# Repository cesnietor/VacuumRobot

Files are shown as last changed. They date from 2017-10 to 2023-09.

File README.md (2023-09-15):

# VacuumRobot
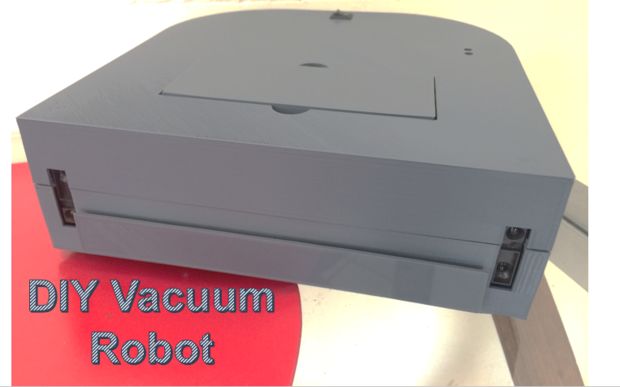
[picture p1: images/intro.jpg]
DIY VacuumRobot


# Created by César Nieto
DIY Vacuum Robot project
An open source project designed to get into the robotics and programming (it is not needed to know how to program).
The full instructions on how to build the robot are on Instructables: 
  https://www.instructables.com/id/Build-Your-Own-Vacuum-Robot/ 

This is my first Vacuum Robot, which it's main purpose is to allow anyone to have a cleaning robot without paying so much money, to learn how they work, to build a nice robot that you can modify, update and program as much as you want, and of course to vacuum all that annoying fluff.

This project is intended to be as easy to build as possible since all the elements and parts are easy to find on Digikey, eBay, Amazon, etc.

The whole chassis was designed in Solidworks so that it could be 3d printed.

Currently it uses an Arduino Uno (if you don't like it too much you can easily change it for another micro controller, I decided to use this since my objective is that anyone could actually build it), micro-metal motors, fan propeller, infrared sensors and respective driver modules.

Another one bites the dust!

Instructions
=====

Step 1: Materials
-----
So, first I will define all the materials that I used and later I will suggest other options with a similar behavior.

**Controllers:**

* 1 x Arduino Uno Board (or similar) ([DigiKey](http://www.digikey.com/product-detail/en/arduino/A000066/1050-1024-ND/2784006))
* 1 x IRF520 MOS FET Driver Module ([Aliexpress](https://aliexpress.com/store/product/0-24VTop-Mosfet-Button-IRF520-MOS-Driver-Module-For-Arduino-MCU-ARM-Raspberry-pie/1185416_32275524365.html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,searchweb201602_3_10000560_10000073_10000561_10000074_10000175_10000507_10000401_10000505_10000068_10000063_10099_10000156_10096_10000569_10000097_10000094_10000090_10000091_10000147_10000144_10084_10000150_10083_10080_10000153_10082_10081_10110_10111_10112_10113_10000535_10114_10000534_10000089_10000086_10000083_10000135_10000080_10078_10079_10073_10000140_10070_10122_10123_10126_10124_10000546_10065_10068_10501_10000132_10000033_10503_10000030_10000126_10000026_10000129_10000023_10000123_432_10060_10062_10056_10055_10054_302_10059_10000120_10000020_10000117_10000013_10103_10102_10000016_10000114_10000111_10052_10053_10050_10107_10051_10106_10000621_10000384_10000101_10000100_10000579_10000104_10000045_10000578_10000108_10000612_10000613_10000390_10000042_10000592_10000039_10000587_10000036_10000389_10000187-10503_10501,searchweb201603_2,afswitch_1,ppcSwitch_4,single_sort_1_default&btsid=23d4dbb7-b390-4b6d-8de8-456e740343d8&algo_expid=c1fe14ed-efb6-4d8b-8aa1-2ef2a833c598-5&algo_pvid=c1fe14ed-efb6-4d8b-8aa1-2ef2a833c598))
* 1 x H-bridge L298 Dual Motor Driver ([Aliexpress](https://aliexpress.com/store/product/Dual-H-Bridge-DC-Stepper-Motor-Drive-Controller-Board-Module-L298N/712084_32273246252.html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,searchweb201602_3_10000560_10000073_10000561_10000074_10000175_10000507_10000401_10000505_10000068_10000063_10099_10000156_10096_10000569_10000097_10000094_10000090_10000091_10000147_10000144_10084_10000150_10083_10080_10000153_10082_10081_10110_10111_10112_10113_10000535_10114_10000534_10000089_10000086_10000083_10000135_10000080_10078_10079_10073_10000140_10070_10122_10123_10126_10124_10000546_10065_10068_10501_10000132_10000033_10503_10000030_10000126_10000026_10000129_10000023_10000123_432_10060_10062_10056_10055_10054_302_10059_10000120_10000020_10000117_10000013_10103_10102_10000016_10000114_10000111_10052_10053_10050_10107_10051_10106_10000621_10000384_10000101_10000100_10000579_10000104_10000045_10000578_10000108_10000612_10000613_10000390_10000042_10000592_10000039_10000587_10000036_10000389_10000187-10503_10501,searchweb201603_2,afswitch_1,ppcSwitch_4,single_sort_1_default&btsid=41cc97c3-c03d-4f3a-9b5a-d7c7f16f9c39&algo_expid=c5bd03f1-c8e0-4179-81da-6a2f469cb3b0-4&algo_pvid=c5bd03f1-c8e0-4179-81da-6a2f469cb3b0))

**Actuators:**

* 2 x Micro Metal Gearmotor HP 6V 298:1 ([DigiKey](http://www.digikey.com/product-detail/en/sparkfun-electronics/ROB-12285/1568-1161-ND/5673747))
* 1 x Micro Metal Gearmotor Bracket Pair ([Pololu](https://www.pololu.com/product/1086))
* 1 x Wheel 42×19mm Pair ([DigiKey](http://www.digikey.com/product-detail/en/sparkfun-electronics/ROB-08899/ROB-08899-ND/5814304))
* 1 x Fan Blower AVC BA10033B12G 12V or similar (BCB1012UH Neato's motor) ([Ebay](http://www.ebay.com/itm/1pc-AVC-BA10033B12G-fan-9733-12V-4-5A-4pin-M3529-QL-/182281112508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), [NeatoOption](http://www.ebay.com/itm/Neato-Vacuum-Fan-and-motor-Impeller-xv-Series-xv-11-xv-14-xv-15-xv-12-xv-21-/201157367856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))

**Sensors:**

* 2 x Sharp Distance Sensor GP2Y0A41SK0F (4 - 30cm) ([DigiKey](http://www.digikey.com/product-detail/en/sharp-microelectronics/GP2Y0A41SK0F/425-2819-ND/3884447))

**Power:**

* 1 x ZIPPY Compact 1300mAh 3S 25C Lipo Pack ([HobbyKing](https://hobbyking.com/en_us/zippy-compact-1300mah-3s-25c-lipo-pack.html))
* 1 x LiPo Battery Charger 3s ([Amazon-Charger](https://www.amazon.com/Turnigy-Compact-Lipo-Charger-100-240v/dp/B00XU4ZR06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))
* 1 x 1k Ohm resistor
* 1 x 2k Ohm small potentiometer

**3d Printing:**

* 3D printer with a minimum printing size of 21 L x 21 W cm .
* PLA Fillament or similar.
* If you don't have, you can print your file on [3DHubs](https://www.3dhubs.com/3dprint).

**Other materials:**

* 20 x M3 bolts with (3mm diameter)
* 20 x M3 nuts
* 2 x #8-32 x 2 IN bolts with nuts and washer.
* 1 x Vaccum bag filter (cloth type)
* 1 x Ball Caster with 3/4″ Plastic or Metal Ball ([Pololu](https://www.pololu.com/product/955))
* 2 pushbuttons
* 1 x On/Off Switch

**Tools:**

* Screw driver
* Soldering Iron
* Pliers
* Scissors
* Cable (3m)

Awesome people share!

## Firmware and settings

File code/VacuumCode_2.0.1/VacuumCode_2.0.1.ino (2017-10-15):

//Code: VaccumCode
//Version: 2.0.1
//Author: Cesar Nieto refer to ces.nietor@gmail.com
//Last change: 19/05/2017
//Changes: Documentation added
#include <math.h> 
////////////PINS////////////////
//Distance Analog Sensors (Sharp)
const int SD1 = 0; //left front sensor
const int SD2 = 1; //right front sensor
const int SD3 = 2; //left side sensor
const int SD4 = 3; //right side sensor

//Battery Voltage input
const int battery = 4;

//IndicatorLED
const int led = 13;

//Fan output
const int fanmotor =  12;      // the number of the LED pin

// Motor1 Right
const int motor1Pin1 = 3;
const int motor1Pin2 = 5;

// Motor2 Left
const int motor2Pin1 = 6;
const int motor2Pin2 = 9;

//Bumper
const int bumper1 = 10;
const int bumper2 = 11;

///////////////Constants////////////////
const float voltageBatCharged = 12.68; // Voltage measured when battery fully charged //Change this
//PWM for the micro metal motors
const int pwmMax = 160;// for 12V  pwmMAx = 170, for 10V output  pwmMax = 140
const int pwmMin = 70;;// for 9V  pwmMin = 128
//Mínimun distance of the sensor
const int minSharp = 30;

// Variables will change:
int bumperState = 0;  // variable for reading the pushbutton status
boolean control = true;
int counter = 0; //   Prevents from being stuck

//////////////CODE/////////////
void setup() {
  //Initialize outputs and inputs
  //Fan motor as output
  pinMode(fanmotor, OUTPUT);
  //Motor1
  pinMode(motor1Pin1, OUTPUT);
  pinMode(motor1Pin2, OUTPUT);
  //Motor2
  pinMode(motor2Pin1, OUTPUT);
  pinMode(motor2Pin2, OUTPUT);
  //LED
  pinMode(led, OUTPUT);
  //INPUTS
  // initialize the pushbutton inputs 
  //Bumper
  pinMode(bumper1, INPUT_PULLUP); 
  pinMode(bumper2, INPUT_PULLUP); 
  //Sensor
  pinMode(SD1, INPUT);
  pinMode(SD2, INPUT);
  pinMode(SD3, INPUT);
  pinMode(SD4, INPUT);
  //Batt
  pinMode(battery, INPUT);
  // Initialize serial
  Serial.begin(9600);    
  ///////////////////////////////Wait////////////////////////////////////////
  //Wait about 5 s and initialize fan if voltage ok
  waitBlinking(5,1); //5 seconds at 1 Hz
  //Crank (initialize the fan because the voltage drops when cranking)
  if(readBattery(battery)>12.1){
    digitalWrite(fanmotor, HIGH); //Turn the Fan ON
    delay(1000); //For 1000ms
  }
  else {
    //do nothing Convention
    }
} 
//////////Functions To Use //////////
void waitBlinking(int n, int frequency){
  //blink for n seconds at frequency hz
  for (int i=1; i <= n; i++){
    for(int j=1; j<=frequency; j++){
      digitalWrite(led, HIGH);   
      delay((1000/frequency)/2);   //Half time on            
      digitalWrite(led, LOW);   
      delay((1000/frequency)/2);   //Half time off
    }
   } 
}
double sdSHARP(int Sensor){
  //Returns the distance in cm
  double dist = pow(analogRead(Sensor), -0.857); // x to power of y
  return (dist * 1167.9);
}
void forwardMotors(int moveTime){  
  //Manipulate direction according the desired movement of the motors
   analogWrite(motor1Pin1, pwmMin); 
   analogWrite(motor1Pin2, 0); //PWM value wher 0 = 0% and 255 = 100%
   analogWrite(motor2Pin1, pwmMin); 
   analogWrite(motor2Pin2, 0); 
   delay(moveTime);
}
void rightMotors(int moveTime){ 
   analogWrite(motor1Pin1, 0); 
   analogWrite(motor1Pin2, pwmMin); 
   analogWrite(motor2Pin1, pwmMin);
   analogWrite(motor2Pin2, 0); 

   delay(moveTime);
}
void leftMotors(int moveTime){ 
   analogWrite(motor1Pin1, pwmMin); 
   analogWrite(motor1Pin2, 0); 
   analogWrite(motor2Pin1, 0);
   analogWrite(motor2Pin2, pwmMin+20); 
   delay(moveTime);
}
void backwardMotors(int moveTime){
   analogWrite(motor1Pin1, 0); 
   analogWrite(motor1Pin2, pwmMin+20);
   analogWrite(motor2Pin1, 0); 
   analogWrite(motor2Pin2, pwmMin+20); 
   delay(moveTime);
}
void stopMotors(){ 
   analogWrite(motor1Pin1, 0);
   analogWrite(motor1Pin2, 0); 
   analogWrite(motor2Pin1, 0); 
   analogWrite(motor2Pin2, 0); 
}
float  readBattery(int input){
  int readInput;
  float voltage;
  readInput = analogRead(input);
  voltage = (((readInput*4.9)/1000)*voltageBatCharged ) / 5; // resolution of analog input = 4.9mV per Voltage 
  Serial.print(" Battery= ");
  Serial.print(voltage);
  return voltage;
  } 
void batteryControl(int input){
  //Turn everything off in case the battery is low
  float v_battery;
  v_battery = readBattery(input);
  if(v_battery<=11.6){ //battery limit of discharge, Don't put this limit lower than  11.1V or you can kill the battery
    control = false;
    }
  else {
    //Do nothing Convention
    }
}
/////////////////////////////////////////////////MAIN CODE//////////////////////////////
void loop(){
  /*  
  Serial.print("SD1= ");
  Serial.print(sdSHARP(SD1));
  Serial.println();
  Serial.print("  SD2= ");
  Serial.print(sdSHARP(SD2));
  Serial.println();
  delay(200);*/
  bumperState = digitalRead(bumper1);
  //Keep the control of the battery automatically turn the fan off
  //If control = true the battery level is ok, otherwise the battery is low.
  batteryControl(battery); //modifies the variable control of the battery is low
  
  if (control){
    digitalWrite(led, HIGH);
    if (sdSHARP(SD1)<=4.3 ){ 
      //If the distance between an object and the left front sensor is less than 4.3 cm or the bumper hits, it will move to the left
      if (counter ==2){ // prevent of being stuck on corners
        counter = 0;
        }
      else {
        //Do nothing Convention
      }
      forwardMotors(100); // approach a bit
      backwardMotors(500); // backward delay of 500ms
      leftMotors(300);
      counter = counter + 2;
      Serial.print("  Turn Left ");
      }
    else if (sdSHARP(SD2)<=4.3){ 
      //If the distance between an object and the right front sensor is less than 4.3 cm, it will move to the right
      if (counter ==1){
        counter = 0;
        }
      else{
        //Do nothing Convention
      }
      forwardMotors(100);
      backwardMotors(500);
      rightMotors(300);
      counter++;
      Serial.print("  Turn Right");
      }
    else if (bumperState==0){
      counter = 0;
      backwardMotors(500); //backward delay of 500ms
      leftMotors(300);
      Serial.print("  Turn Left ");
      }
    else {
      if(counter==3){ //Corner
        leftMotors(1000);
        counter = 0;
        }
      else {
        forwardMotors(0);
      }
      Serial.print("  Move Forward");
      }
  }
  else if (!control){
    //If the battery is low, turn everything off
    digitalWrite(fanmotor, LOW); //Turn the Fan OFF
    stopMotors();
    Serial.print(" Low Battery! ");
    Serial.println();
    waitBlinking(1,3);  //blink as warning 3hz in a loop
    }
  Serial.println();
}

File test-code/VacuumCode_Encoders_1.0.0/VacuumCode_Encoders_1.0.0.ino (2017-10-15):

//Code: VaccumCode_Encoders
//Version: 1.0.0
//Author: Cesar Nieto refer to ces.nietor@gmail.com
//Last change: 04/10/2017
//Last Changes: Code added to support Pololu Motor Encoders, pins have been changed.
//              A PD controller is used to control the speed of the motors.                
#include <math.h> 
////////////PINS////////////////
// Distance Analog Sensors (Sharp)
#define SD1     (0)   //left front sensor
#define SD2     (1)   //right front sensor
#define SD3     (2)   //left side sensor
#define SD4     (3)   //right side sensor
// Battery Voltage input
#define battery     (4)   //Analog
// IndicatorLED
#define led         (13)
// Fan output
#define fanmotor    (12)  // the number of the LED pin
// Motor1 Right
#define motor1Pin1  (9)
#define motor1Pin2  (10)
#define encodPinA1  (2)   // encoder A pin, interrupt pin of Arduino Uno
#define encodPinB1  (4)   // encoder B pin, read motor direction
// Motor2 Left
#define motor2Pin1  (5)
#define motor2Pin2  (6)
#define encodPinA2  (3)   // encoder A pin, interrupt pin of Arduino Uno
#define encodPinB2  (7)   // encoder B pin, read motor direction
// Bumper
#define bumper1     (8)
#define bumper2     (11)
// PWM for the micro metal motors //Values to delete soon since use of PID
#define pwmMax      (160) 
#define pwmMin      (0)  
// PID loop time
#define LOOPTIME  (100)                     

///////////////Constants////////////////
const float voltageBatCharged = 12.68; // Voltage measured when battery fully charged //Change this
const float batteryLimitDischarge = 11.6; // Safe value to not kill the Battery

// Variables will change:
int bumperState = 0;  // variable for reading the pushbutton status
int counter = 0; //   Prevents from being stuck
boolean control = true;
boolean printOnce = true; //For debugging

unsigned long lastMilli = 0;    // loop timing 
unsigned long lastMilliPrint = 0;
unsigned long lastErrorMilli = 0;
//Motor 1
float speed_req1 = 60.0;            // speed (Set Point)
float speed_act1 = 0.0;             // speed (actual value)
int PWM_val1 = 0;               // (25% = 64; 50% = 127; 75% = 191; 100% = 255)
volatile long count_1 = 0;      // rev counter
//Motor 2
float speed_req2 = 60.0;
float speed_act2 = 0.0;
int PWM_val2 = 0;
volatile long count_2 = 0;

float Kp =   0.6;// 0.65;        // PID Proportional control Gain   (Good values as well: 0.5)     
float Kd =   0.0;// 0.005;       // PID Derivitave control Gain

//////////////CODE/////////////
void setup() {
  Serial.begin(9600); // Initialize serial
  //Initialize outputs and inputs
  //Fan motor as output
  pinMode(fanmotor, OUTPUT);
  //Motor1
  pinMode(motor1Pin1, OUTPUT);
  pinMode(motor1Pin2, OUTPUT);
  //Motor2
  pinMode(motor2Pin1, OUTPUT);
  pinMode(motor2Pin2, OUTPUT);
  //LED
  pinMode(led, OUTPUT);
  //INPUTS
  //Initialize the pushbutton inputs 
  //Motor encoders
  pinMode(encodPinA1, INPUT_PULLUP); 
  pinMode(encodPinB1, INPUT_PULLUP);
  pinMode(encodPinA2, INPUT_PULLUP); 
  pinMode(encodPinB2, INPUT_PULLUP); 
  //Bumper
  pinMode(bumper1, INPUT_PULLUP); 
  pinMode(bumper2, INPUT_PULLUP); 
  //Sensor
  pinMode(SD1, INPUT);
  pinMode(SD2, INPUT);
  pinMode(SD3, INPUT);
  pinMode(SD4, INPUT);
  //Batt
  pinMode(battery, INPUT);
  //Encoder Interrupt executes rencoder_# function when falling edge of the signal
  //Refer to: https://www.arduino.cc/en/Reference/AttachInterrupt
  //Arduino UNO only has 2 external interrupts
  attachInterrupt(0, rencoder_1, FALLING);  //Pin 2 of Arduino Uno
  attachInterrupt(1, rencoder_2, FALLING);  //Pin 3 of Arduino Uno
    
  ///////////////////////////////Wait////////////////////////////////////////
  //Wait about 5 s and initialize fan if voltage ok
  Serial.println("Starting...");
  waitBlinking(3,1); //5 seconds at 1 Hz
  //Crank (initialize the fan because the voltage drops when cranking)
  if(readBattery(battery)>12.1){
    digitalWrite(fanmotor, HIGH); //Turn the Fan ON
    delay(500); //For 1000ms
  }
  else {
    //do nothing Convention
    }
} 
/////////////////////////////////////////////////MAIN CODE//////////////////////////////
void loop(){
  //Keep the control of the battery automatically turn the fan off
  //If control = true the battery level is ok, otherwise the battery is low.
  batteryControl(battery); //modifies the variable control of the battery is low
  setMotors(); //Set pwm of each motor according to the actual speed
  controlRobot(); // Execute all conditions to move
  printMotorsInfo();
}

//////////Functions To Use //////////
//PORTD, containts Digital pins 0-7, 4 and 7 used to consider the direction of each motor. (PIND is for read only) 
void rencoder_1()  {                                  // pulse and direction, direct port reading to save cycles
  if (PIND & 0b00010000)     count_1++;                // if(digitalRead(encodPinB1)==HIGH)   count ++;
  else                      count_1--;                // if (digitalRead(encodPinB1)==LOW)   count --;
}

void rencoder_2()  {                                  // pulse and direction, direct port reading to save cycles
  if (PIND & 0b10000000)     count_2++;                // if(digitalRead(encodPinB2)==HIGH)   count ++;
  else                      count_2--;                // if (digitalRead(encodPinB2)==LOW)   count --;
}
void waitBlinking(int n, int frequency){
  //blink for n seconds at frequency hz
  for (int i=1; i <= n; i++){
    for(int j=1; j<=frequency; j++){
      digitalWrite(led, HIGH);   
      delay((1000/frequency)/2);   //Half time on            
      digitalWrite(led, LOW);   
      delay((1000/frequency)/2);   //Half time off
    }
   } 
}
double sdSHARP(int Sensor){
  //Returns the distance in cm
  double dist = pow(analogRead(Sensor), -0.857); // x to power of y
  return (dist * 1167.9);
}
float  readBattery(int input){
  int readInput;
  float voltage;
  readInput = analogRead(input);
  voltage = (((readInput*4.9)/1000)*voltageBatCharged ) / 5; // resolution of analog input = 4.9mV per Bit resolution
  Serial.print(" Battery= ");
  Serial.print(voltage);
  return voltage;
  } 
void batteryControl(int input){
  //Turn everything off in case the battery is low
  float v_battery;
  v_battery = readBattery(input);
  if(v_battery<=batteryLimitDischarge){ //battery limit of discharge, Don't put this limit lower than  11.1V or you can kill the battery
    control = false;
    }
  else {
    //Do nothing Convention
    }
}
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
